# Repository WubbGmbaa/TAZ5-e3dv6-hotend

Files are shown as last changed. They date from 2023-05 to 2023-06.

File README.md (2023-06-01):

# TAZ5-e3dv6-hotend
Direct drive extruder using generic e3dv6 hotend parts for 1.75mm conversion on Lulzbot TAZ 5

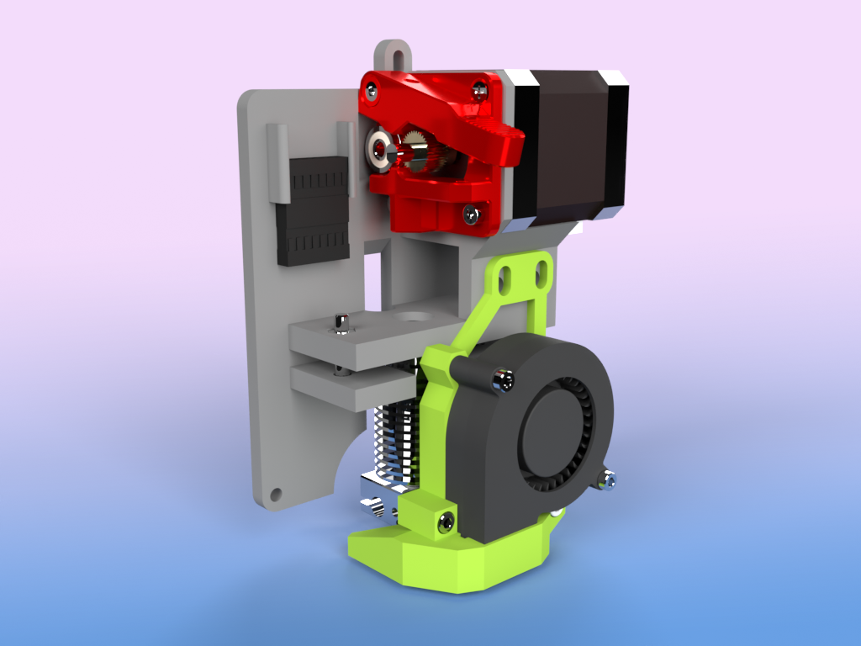
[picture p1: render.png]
Extruder Render


CONFIG contains slicer presets. DOCS contains [assembly instructions](./DOCS/INSTRUCTIONS.MD).

Files are also mirrored on [Thingiverse](https://www.thingiverse.com/thing:6055612) and [Printables](https://www.printables.com/model/495617-taz-5-175mm-conversion-using-e3d-v6)

Part cooling fan adapted from [E3D v6 CFD optimized adjustable part cooling duct](https://www.thingiverse.com/thing:3590464) by DaVinci2000 on Thingiverse
Mount adapted from original LulzBot part [extruder_mount_hex](https://download.lulzbot.com/TAZ/5.0/production_parts/printed_parts/extruder_mount_hex/)

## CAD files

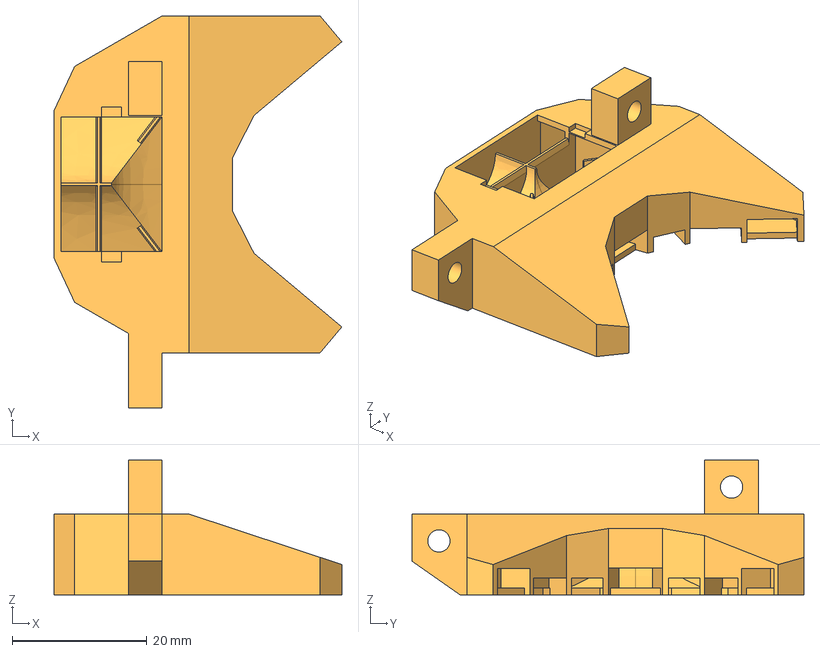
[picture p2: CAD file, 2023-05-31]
STEP/PartFanDuct.stp
42.7 x 58.2 x 20.0 mm

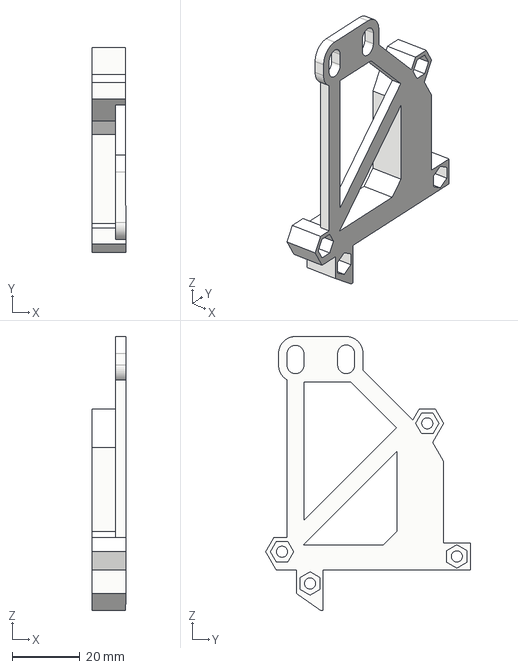
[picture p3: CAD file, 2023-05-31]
STEP/FanBracket.stp
9.95 x 60.6 x 81.1 mm

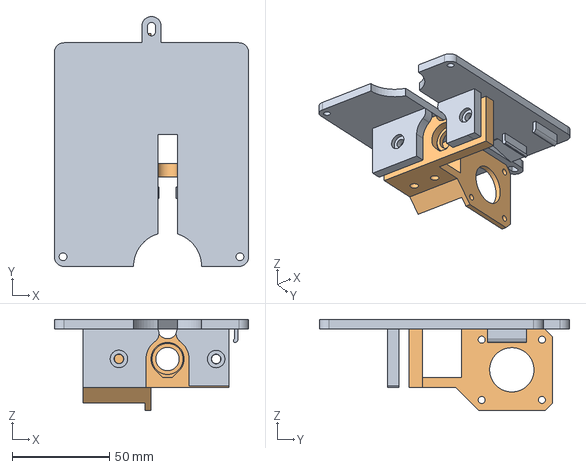
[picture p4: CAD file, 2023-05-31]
STEP/ExtruderPlate.stp
100.0 x 128.6 x 47.0 mm

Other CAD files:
STL/ExtruderPlate.stl
STL/FanBracket.stl
STL/PartFanDuct.stl

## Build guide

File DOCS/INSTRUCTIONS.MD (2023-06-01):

# Assembly Instructions
### Materials
You will need the following to assemble the hotend
* A generic e3d v6 hotend. Clones are available online for around $20, but make sure to get one with a 24v heater cartridge
* Two M3x20 bolts, two M3x10 bolts, and four M3 nuts (for DaVinci2000's part cooler shroud)
* A 5015 "squirrel cage" blower fan (for the part cooler)
* Some short wires, about 22AWG
* Pin headers
    * a 4-pin header for the stepper, a 2-pin header for the part cooler fan, and a 2x8 header for the TAZ hotend connector - I used two smaller headers side-by-side, a 2x3 for the thermistor and a 2x5 for everything else
* The old hotend/extruder from your TAZ 5
* A generic bowden extruder
* Some bowden tube (58mm long)
### Prep
1. Print inlcuded stl files, ideally in PETG or ABS.
2. Remove the extruder and french cleat from the TAZ and dissassemble, keeping all hardware handy.
3. Assemble the e3d v6 hotend in its entirety, routing the hotend cartridge and thermistor cables sideways away from the nozzle, then loosely upwards as shown. Attach the heatsink fan shroud on the opposite side from the cartridge and thermistor cables.
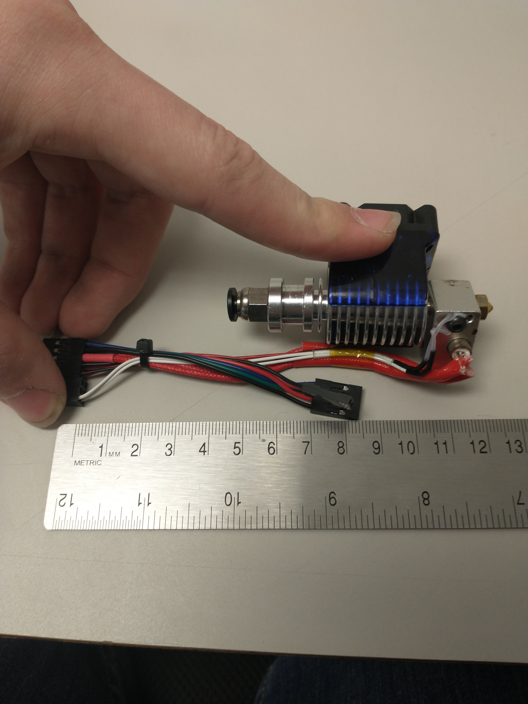
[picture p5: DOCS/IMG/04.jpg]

4. Cut and splice wires to length as shown below. Optionally, re-splice a new 4-pin connector onto the stepper motor - I did this to tidy the wires, leaving about 1 inch to the stepper.
(Cable diagram coming soon, reference above for now)
    * Note that I terminated the stepper differently from LulzBot - the diagram shows the correct pinout for LulzBot's stepper, but the pictures show my wiring.
5. Heat-set two 5mm M3 inserts in the holes on the main plate (inserts can be salvaged from the TAZ's old part cooler mount)
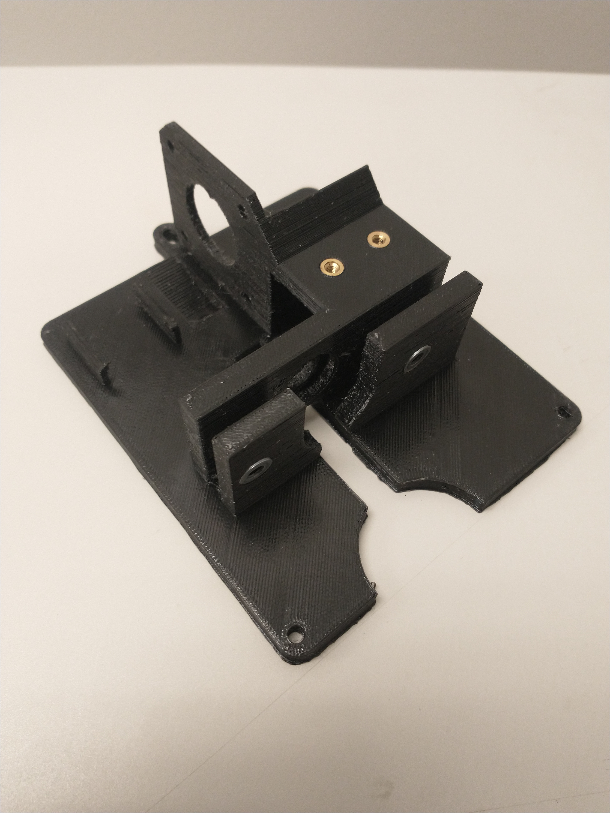
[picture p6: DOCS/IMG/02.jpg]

### Mounting the e3d v6 hotend
1. Insert the hotend connector through the back side of the plate so that it comes out above the extruder mount
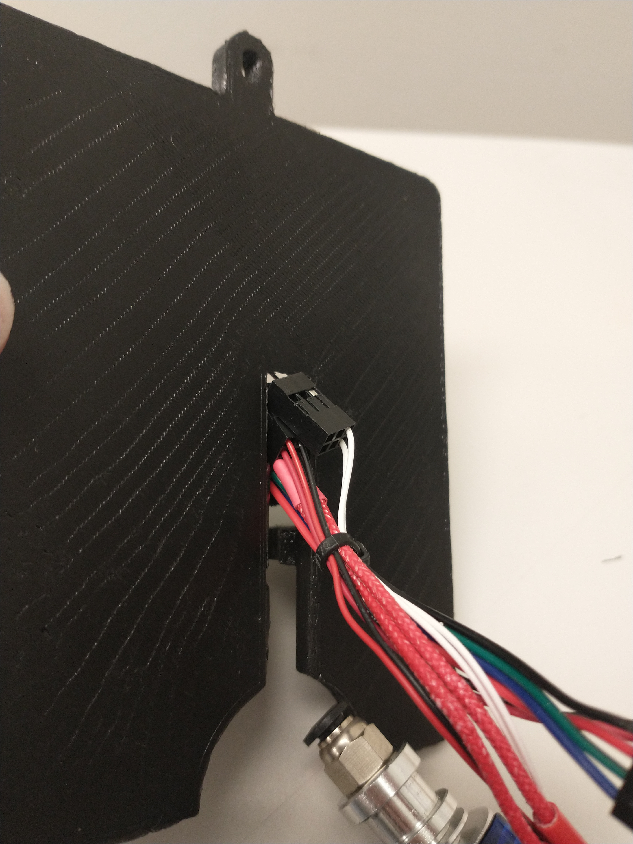
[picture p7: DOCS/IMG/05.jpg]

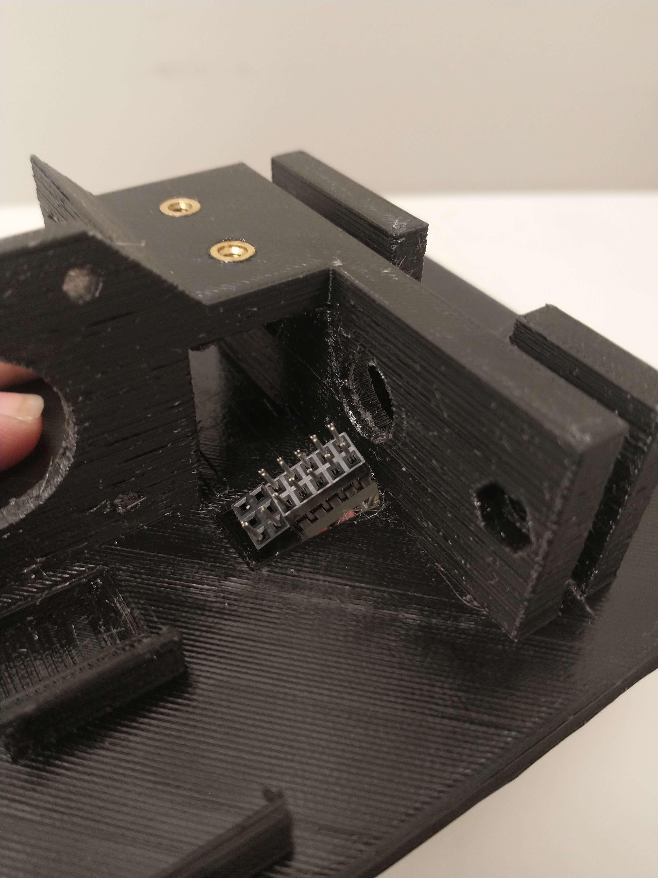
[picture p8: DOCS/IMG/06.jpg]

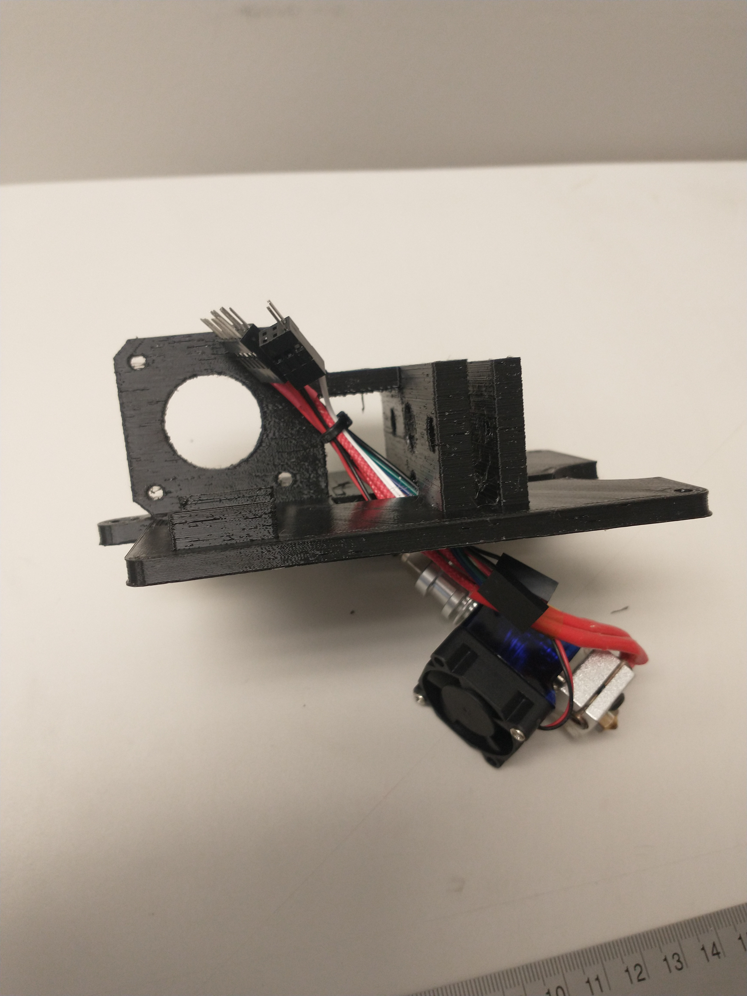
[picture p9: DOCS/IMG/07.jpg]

2. Pull through the connectors for the part cooling fan and stepper.
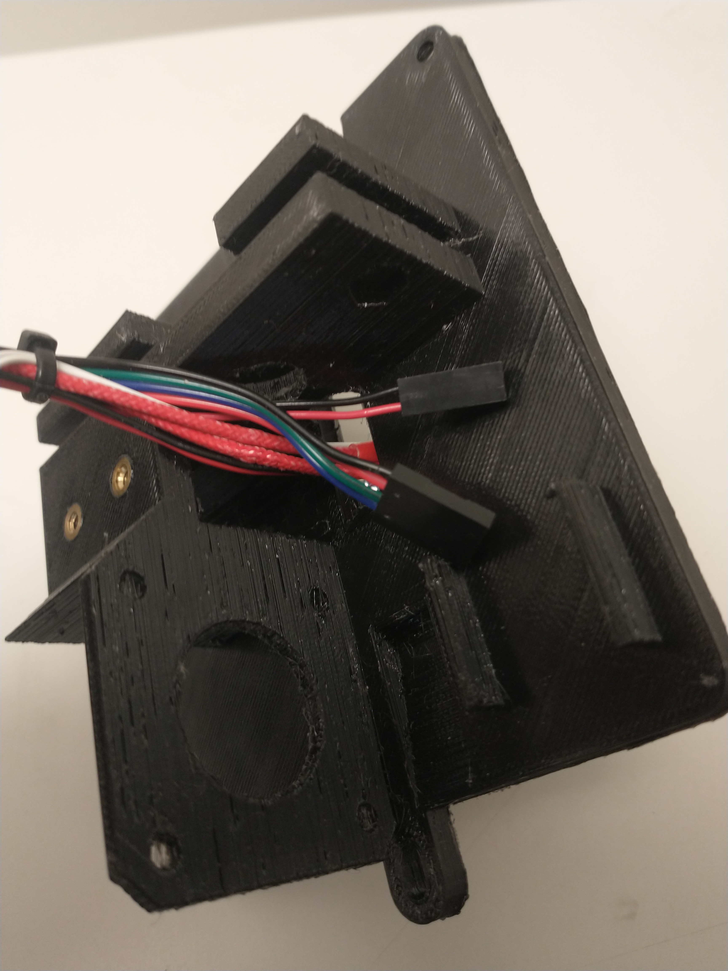
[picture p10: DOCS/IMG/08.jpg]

3. Tuck the hotend under the bottom of the plate, and upwards loosely into its mount. The wires should tuck into the channel along the back.
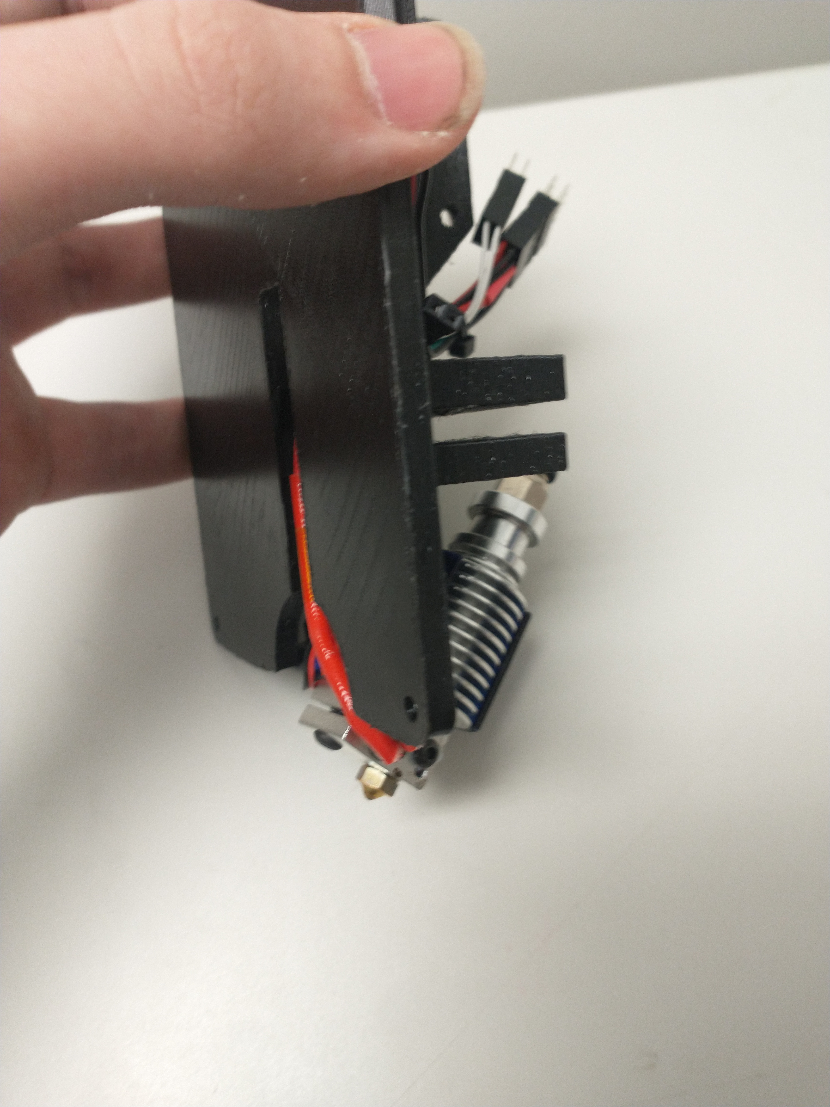
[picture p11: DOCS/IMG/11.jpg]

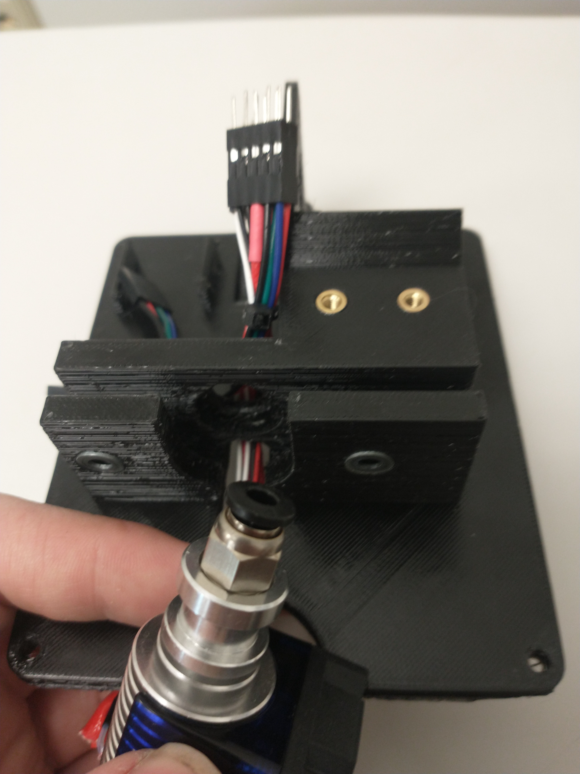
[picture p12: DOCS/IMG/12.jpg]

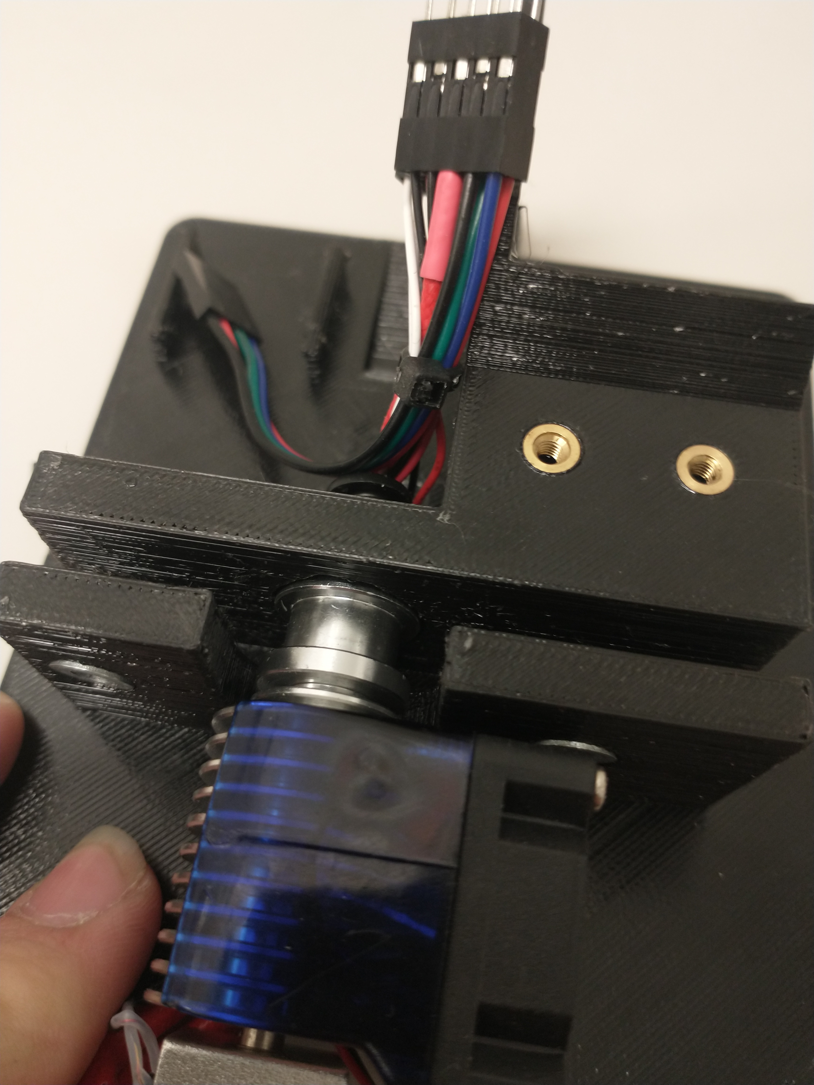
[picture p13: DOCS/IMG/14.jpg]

4. Insert the aluminum bracket from the original extruder, upside-down, into the slot between the "shelves" of the hotend mount. It should push the hotend snugly into the top shelf cutout.
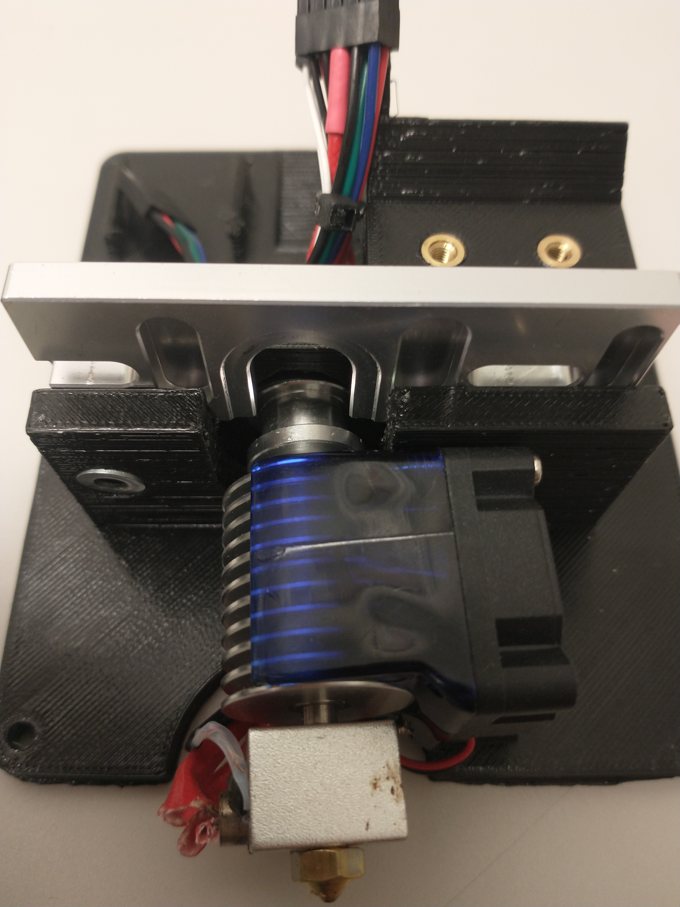
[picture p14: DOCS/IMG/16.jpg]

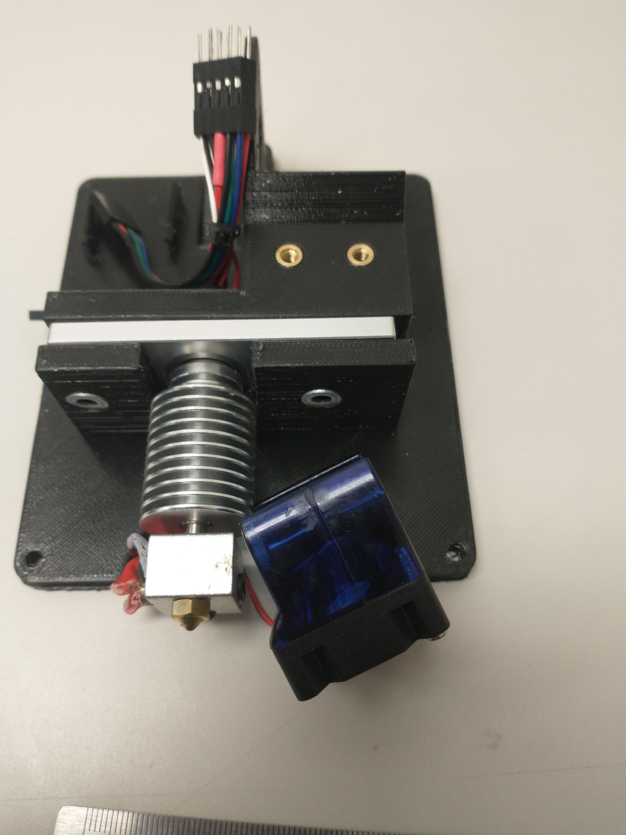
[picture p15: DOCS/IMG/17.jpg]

5. Insert the two larger (M4?) bolts, nuts, and washers from the original extruder to hold the bracket in place. You may need to temporarily un-clip the fan from the heatsink to insert the right-side bolt. The fan should just clear the head of the bolt when clipped back on.
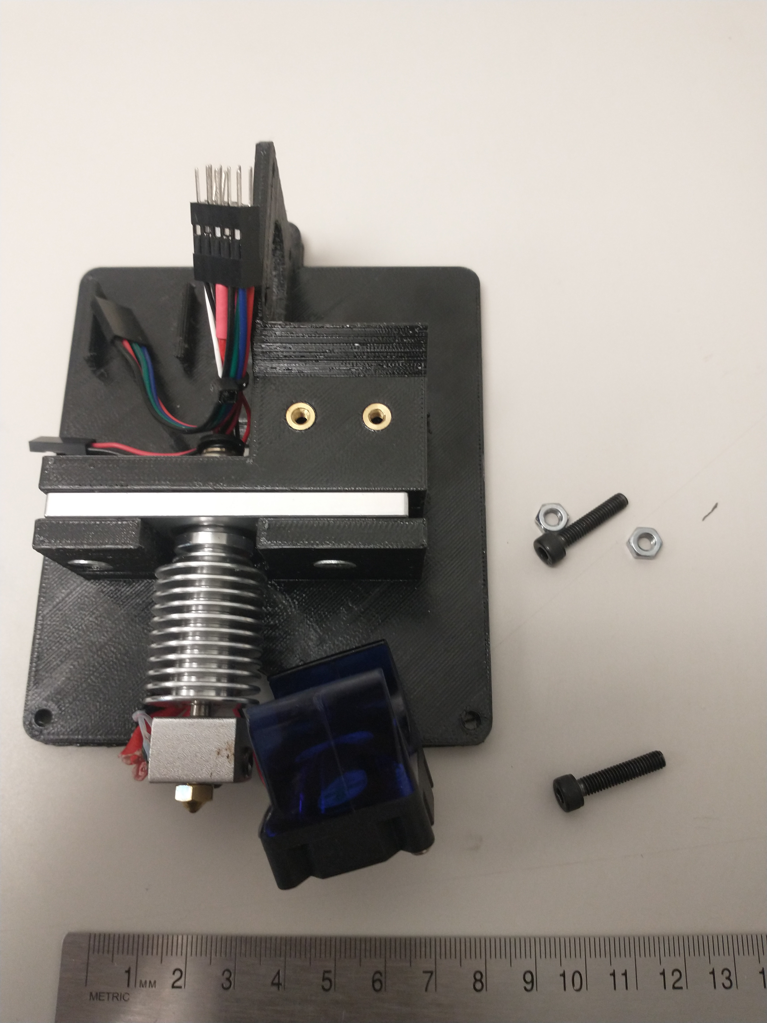
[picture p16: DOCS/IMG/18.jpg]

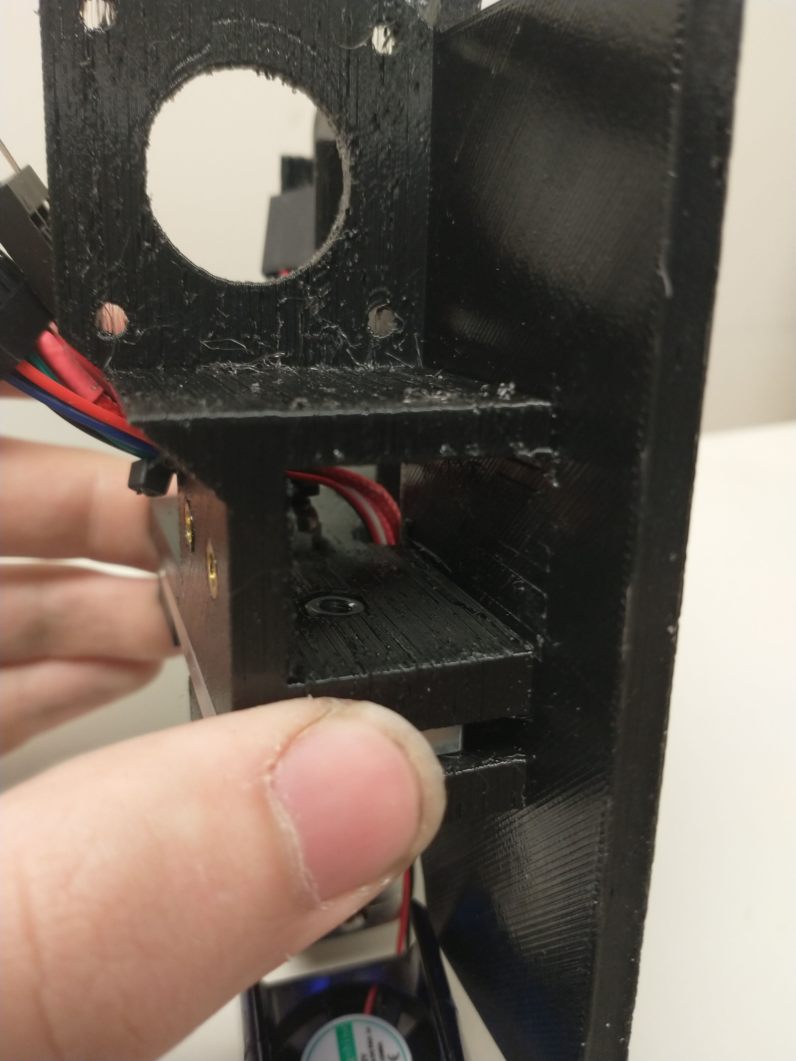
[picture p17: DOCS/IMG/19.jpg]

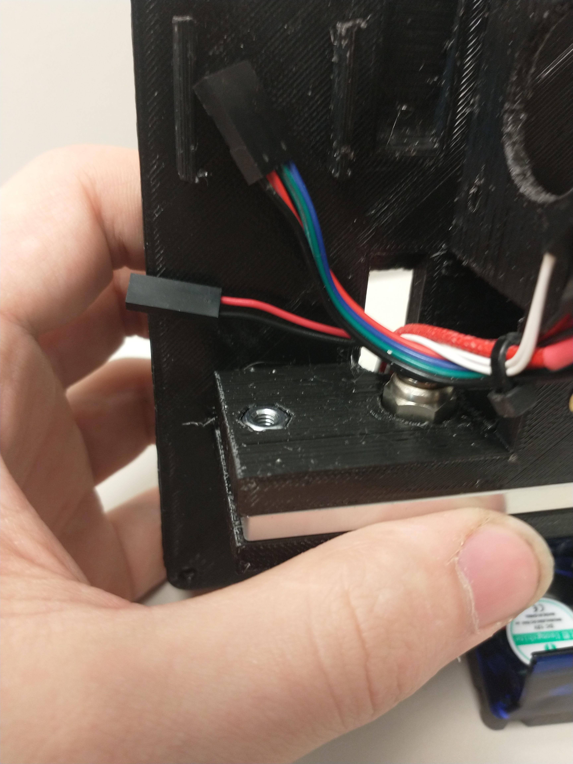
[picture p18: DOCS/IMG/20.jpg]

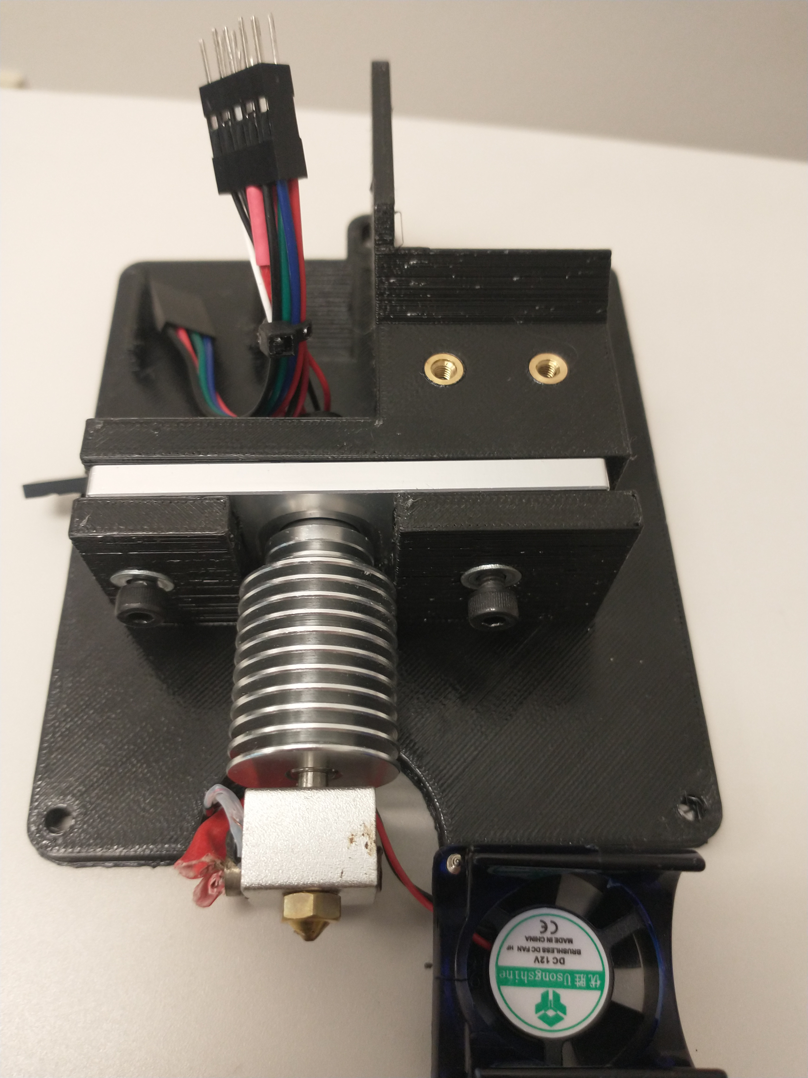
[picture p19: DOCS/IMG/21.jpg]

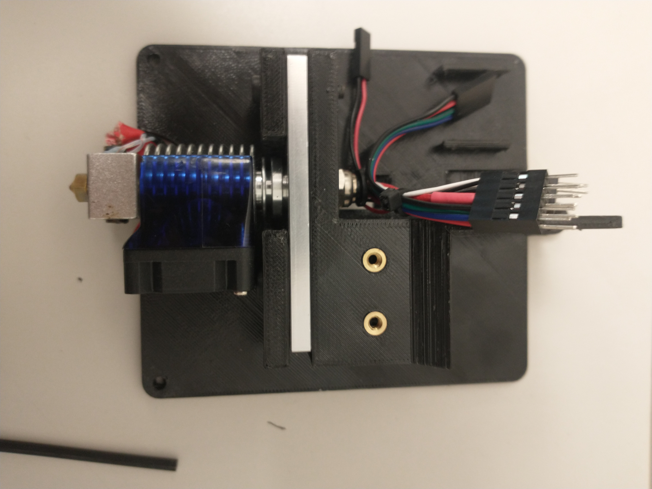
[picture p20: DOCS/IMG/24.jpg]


### Mounting the extruder
1. Route the connectors for the stepper motor and part cooler fan behind the stepper support pillar.
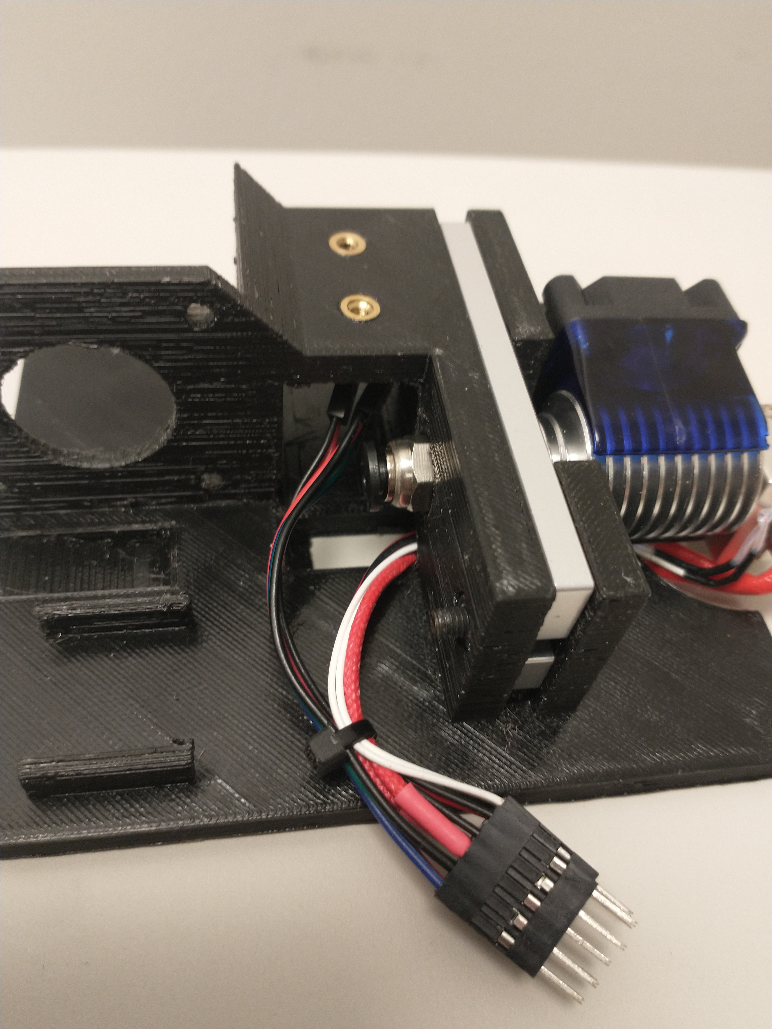
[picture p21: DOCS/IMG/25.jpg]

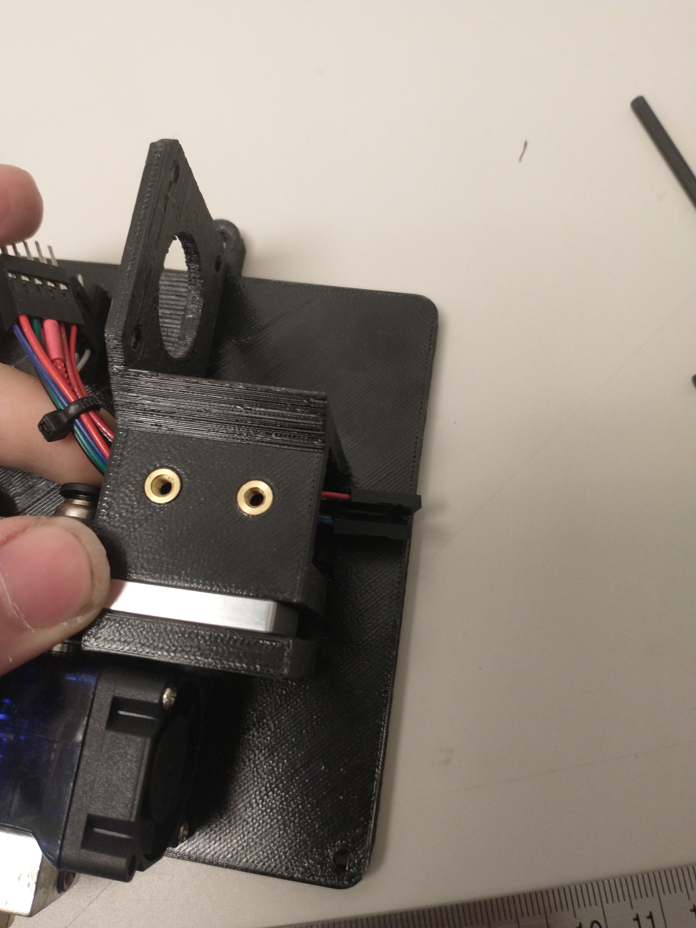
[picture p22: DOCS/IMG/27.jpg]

2. Cut the bowden tube to 58mm and straigthen. I used a vee router bit to chambfer the inside edge connecting to the extruder.
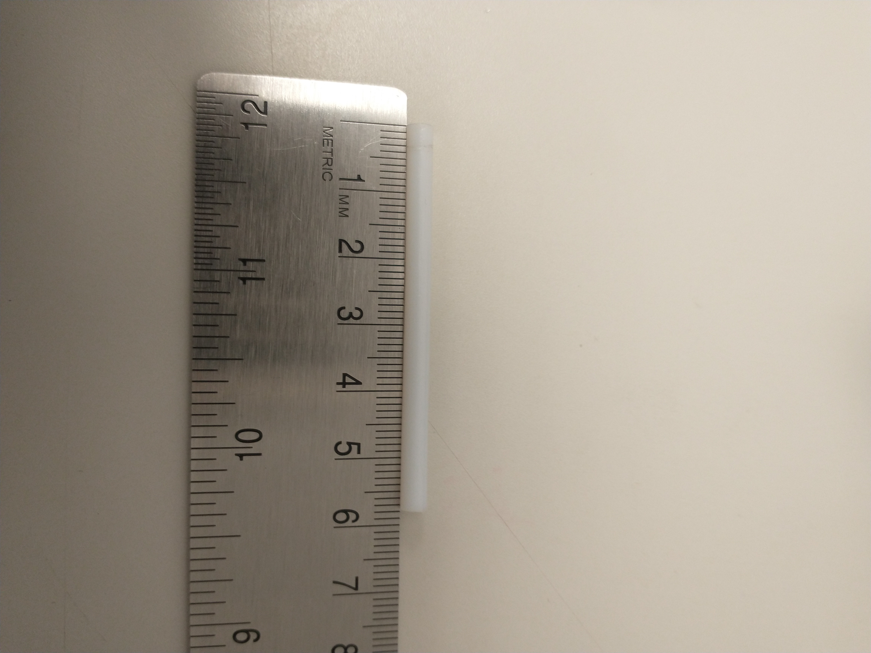
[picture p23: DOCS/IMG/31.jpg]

3. Partially assemble the extruder - attach the bolt for the spring and the PTFE connector.
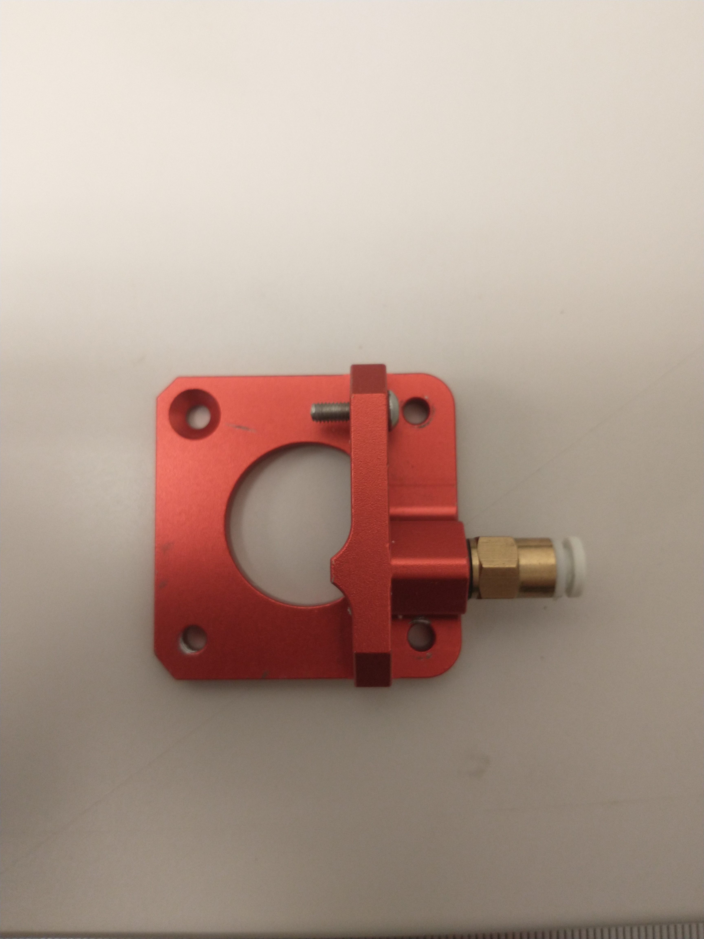
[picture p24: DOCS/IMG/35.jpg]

4. Insert the bowden tube fully into the heatsink, and slide the extruder body onto the protruding ~1cm end. The extruder body should line up with the stepper mounting holes, with ~2mm to release the PTFE connectors if needed.
Step 4 Assembly View
Step 4 Assembly View
5. Slide the stepper into position, wires pointing down. Slide the extruder gear onto the stepper shaft and tighten its set screws.
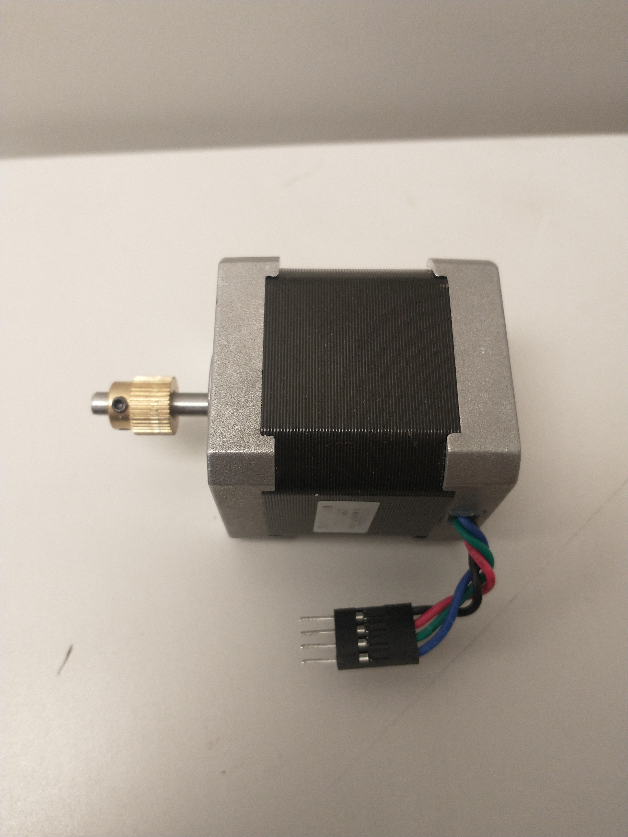
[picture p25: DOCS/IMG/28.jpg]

Step 5 Assembly View
6. Insert the flat-head bolt and the two short cap-head bolts for the extruder and tighten onto the stepper.
Step 6 Assembly View
7. Attach the extruder lever using its long bolt. Squeeze the spring into position.
Step 7 Assembly View
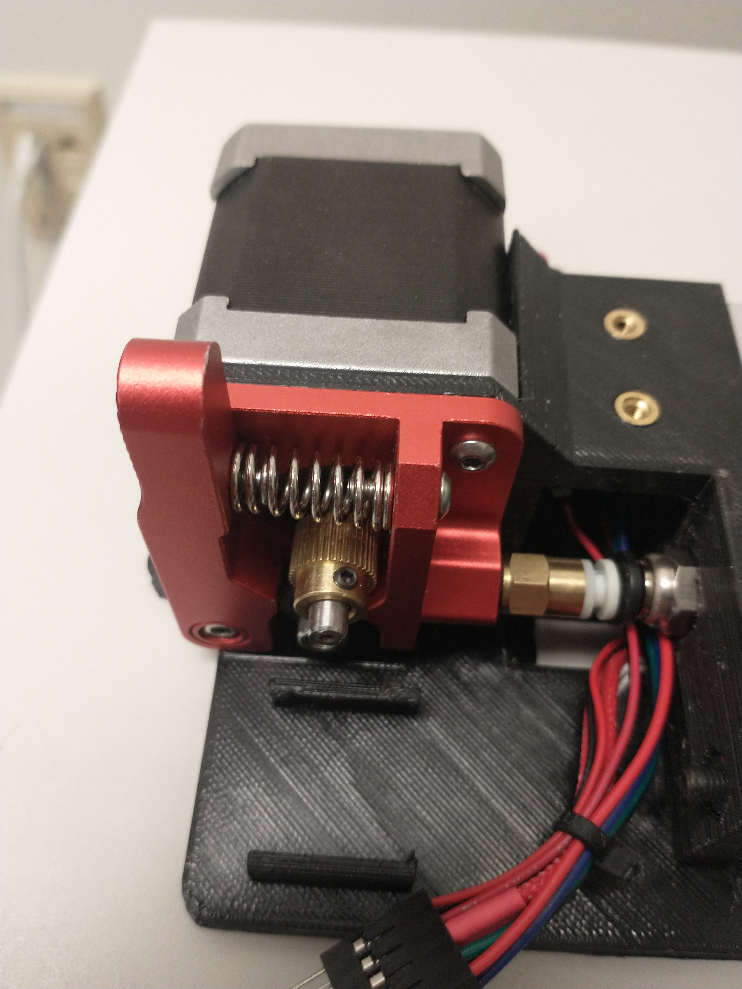
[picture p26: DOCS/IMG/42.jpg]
Step 7 Assembly View

8. Connect the extruder to the wire harness.
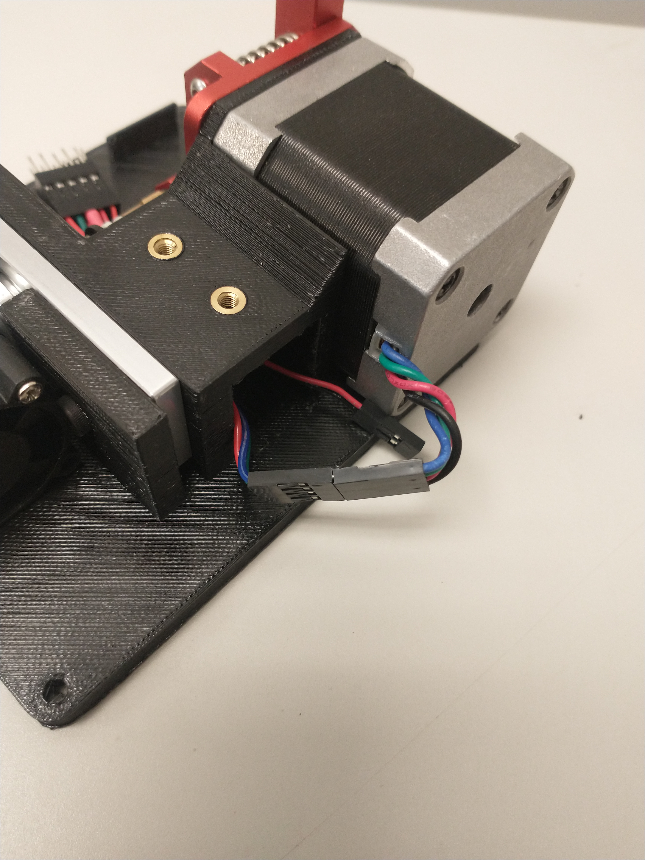
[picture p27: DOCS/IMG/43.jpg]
Step 8 Assembly View


### Mounting the assembly onto the TAZ
1. Insert the top bolt, hanging the plate off of it. Slide the plate up and insert the bottom two corner bolts (from the french cleat used in the prior design). The middle two bolts will not be used. Tighten all three.
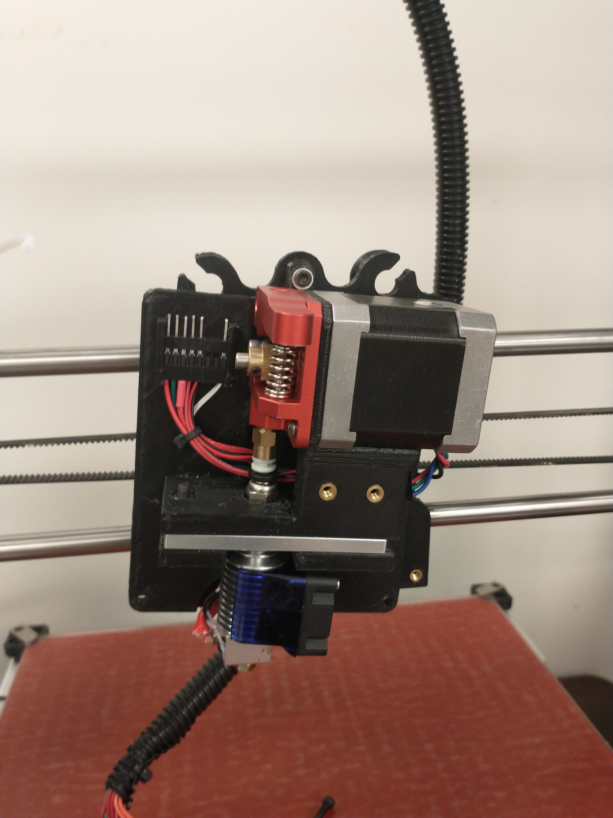
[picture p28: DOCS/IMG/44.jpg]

Step 1 Assembly View
2. Connect the hotend cable and slide into the upper-left corner mount.
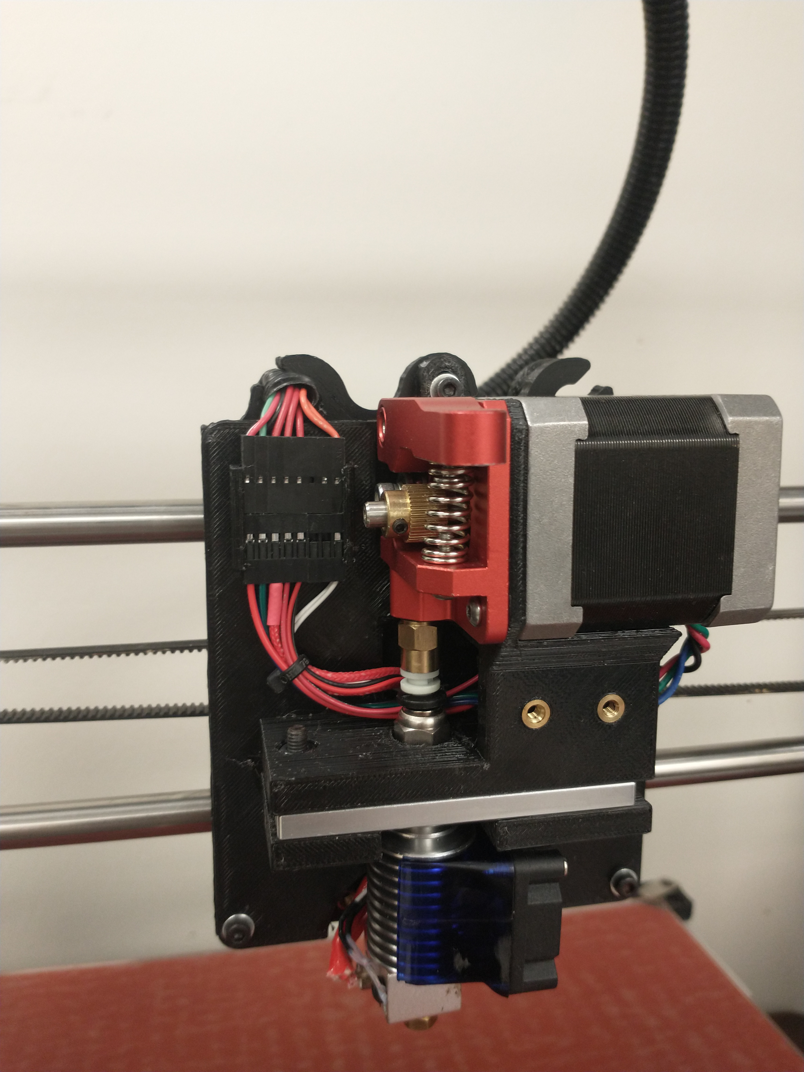
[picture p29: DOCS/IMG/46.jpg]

3. Calibrate your z endstop bolt. You will likely have to remove the spring and washers - I used some poster putty to fix it in place without them.
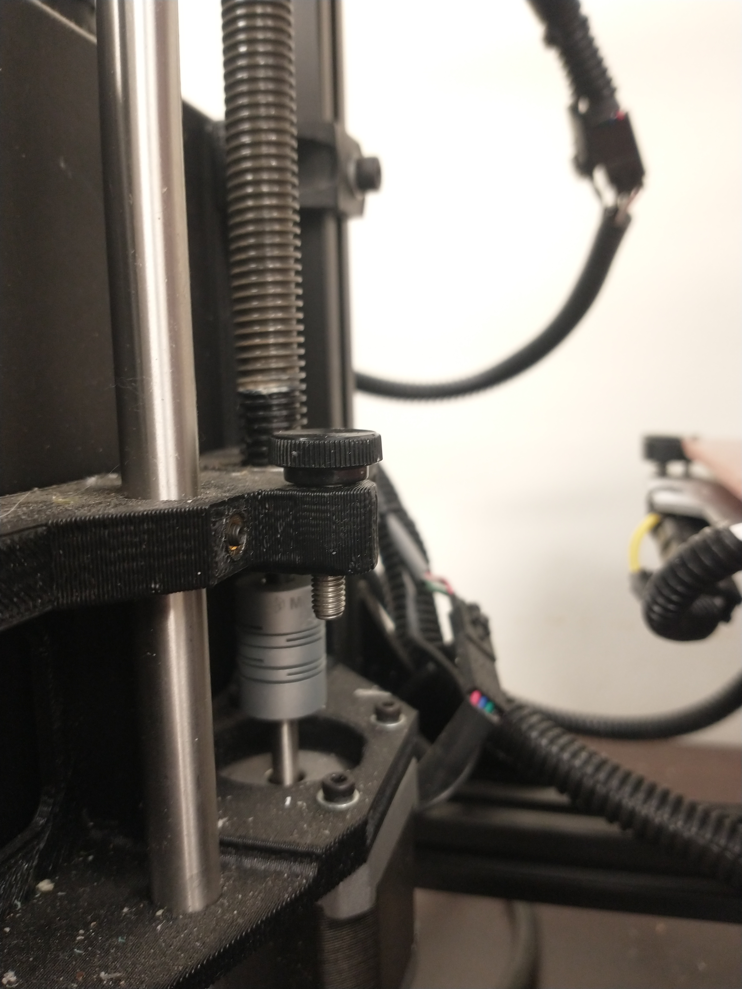
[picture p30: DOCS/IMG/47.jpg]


### Mounting the part cooler
1. If it doesn't already have one, crimp a pin header onto the fan. I left my fan's wires about 65mm long.
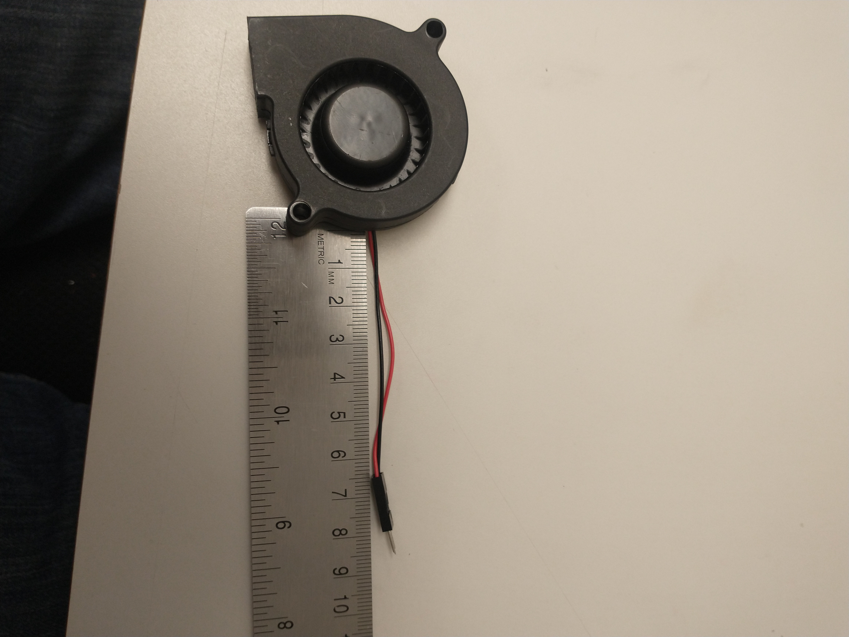
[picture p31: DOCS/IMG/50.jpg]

2. Insert the fan into the shroud. It should fit snug.
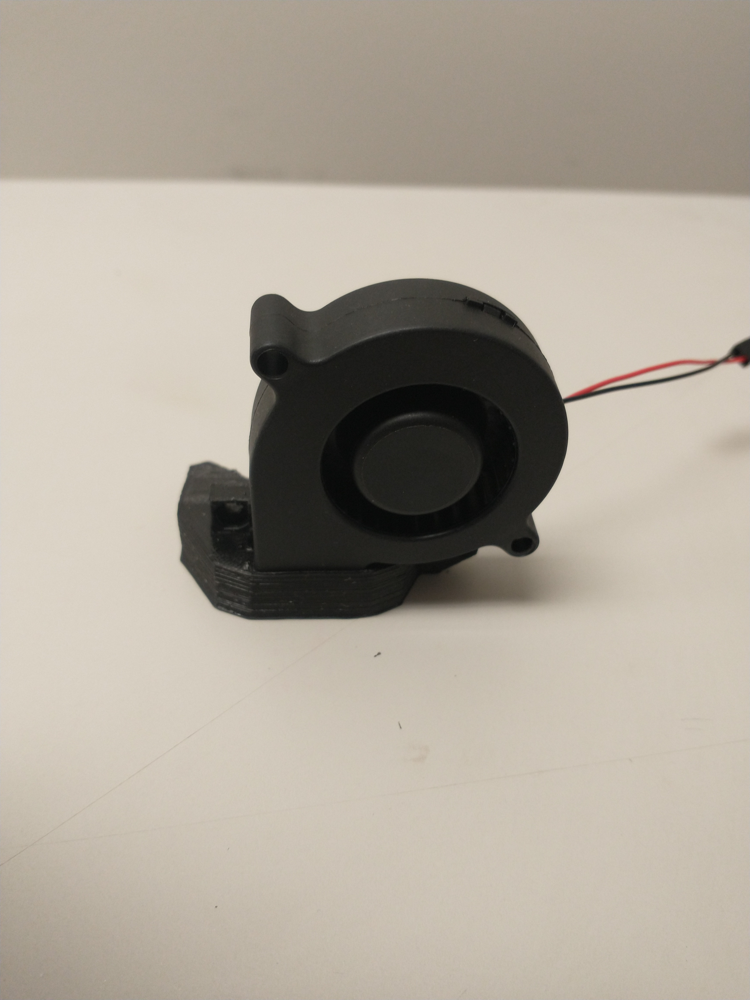
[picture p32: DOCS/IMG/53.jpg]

3. Using the M3x10 and M3x20 bolts and M2 nuts, attach the fan mount bracket as shown. The longer bolts will attach the fan, and the shorter will connect to the shroud.
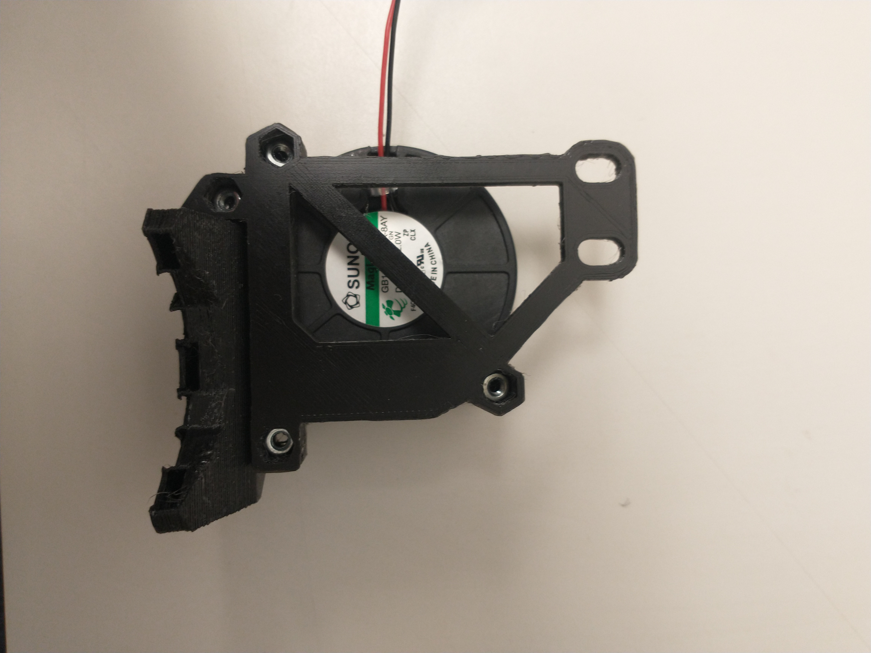
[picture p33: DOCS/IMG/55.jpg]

4. Using the bolts from the original part cooling shroud, attach the fan bracket to the extruder plate. Adjust height as needed, then tighten the bolts.
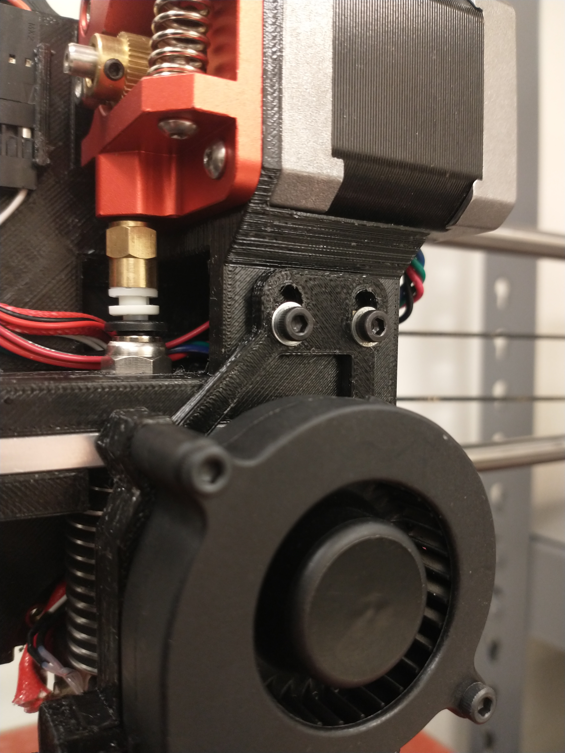
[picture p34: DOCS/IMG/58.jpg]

5. Plug the fan into the wire harness.
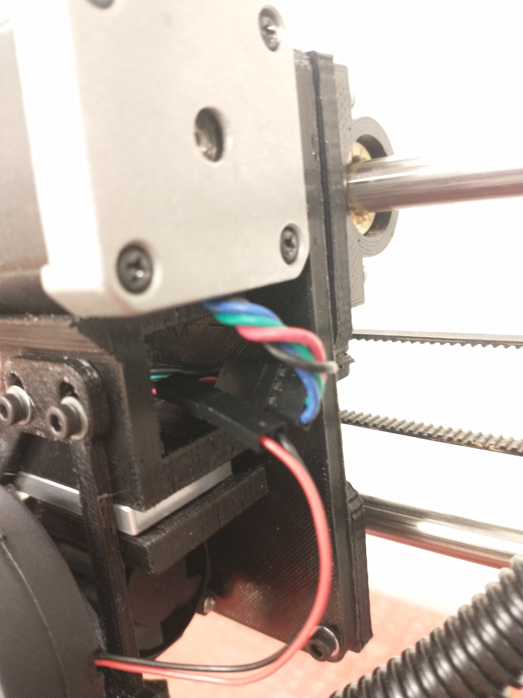
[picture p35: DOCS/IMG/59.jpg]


### Config Changes
1. On the TAZ, under Configuration > Advanced Settings, set your Esteps/mm. I set mine to +0098.0 but yours may be slightly different depending on the extruder gear - see [this guide](https://all3dp.com/2/extruder-calibration-calibrate-e-steps/) for help calibrating.
2. Make sure to change the filament diameter in your preferred slicer - the repo contains a config for PrusaSlicer in "CONFIG/" (which I believe will work in regular Slic3r), and I will add one for Cura soon.

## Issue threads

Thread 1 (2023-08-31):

FanBracket bolt holes misaligned

WubbGmbaa, 2023-08-31:
Bolts to mount onto ExtruderPlate are just within hotend level tolerance at highest setting, need to be adjusted down 1-2mm

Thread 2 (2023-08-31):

FanBracket too flexible

WubbGmbaa, 2023-08-31:
Bracket flexes along Y axis, causing one end of duct to sag slightly in Z. Can catch on TAZ heatbed corner brackets if printing low near corners.

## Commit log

2023-04-06 Initial commit, add prototype cad files
    initial cad files for Inventor, to be exported as step. Some files may need redesigned
    [Extrusor - P1 -MK8^MK8 Red Extruder Bowden.ipt, Extrusor - P2 -MK8^MK8 Red Extruder Bowden.ipt, Extrusor - P3 -MK8^MK8 Red Extruder Bowden.ipt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]
2023-05-31 combined main extruder parts into one piece, added fan mount, reorganized project, replaced .ipt inventor files with step files, added stls
    [ExtruderPlate.stl, ExtruderPlate.stp, Extrusor - P1 -MK8^MK8 Red Extruder Bowden.ipt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]
2023-06-01 Added assembly instructions
2023-06-01 Added missing step for fan connector
